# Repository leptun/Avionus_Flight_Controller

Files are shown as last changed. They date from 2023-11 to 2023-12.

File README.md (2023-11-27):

# Avionus_Flight_Controller

This repo contains the mainboard for the Avionus project, a semi-autonomous plane/drone. The project is work in progress 🚧.

Features:
- STM32F722ZE MCU with hardware float, 512KB of flash and 256KB of RAM
- 16MB total of external dual-mode QuadSPI (QPI) flash memory with XIP capability
- Full size SD card slot
- GPS (ublox MAX-M10S) with onboard antenna
- 9dof IMU ICM-20948
- LIDAR distance sensors with headers for:
  - LIDAR07-100W
  - VL53L1X
- 16 servo outputs (including at least one UART connection)
- RC remote input:
  - PPM interface
  - iBus interface
- LoRa 868MHz module using Semtech SX1262
- USB 2.0 FS with Type C connector (device only)
- Independent power domanins for the peripherals:
  - Power domains voltage measurement and monitoring
  - Current measurement of critical power domains
  - Very low power shutdown with wake from RTC
  - ESD protection of all IO
- STDC14 debugging header for STLINK-V3:
  - SWD
  - JTAG
  - SWO
  - UART

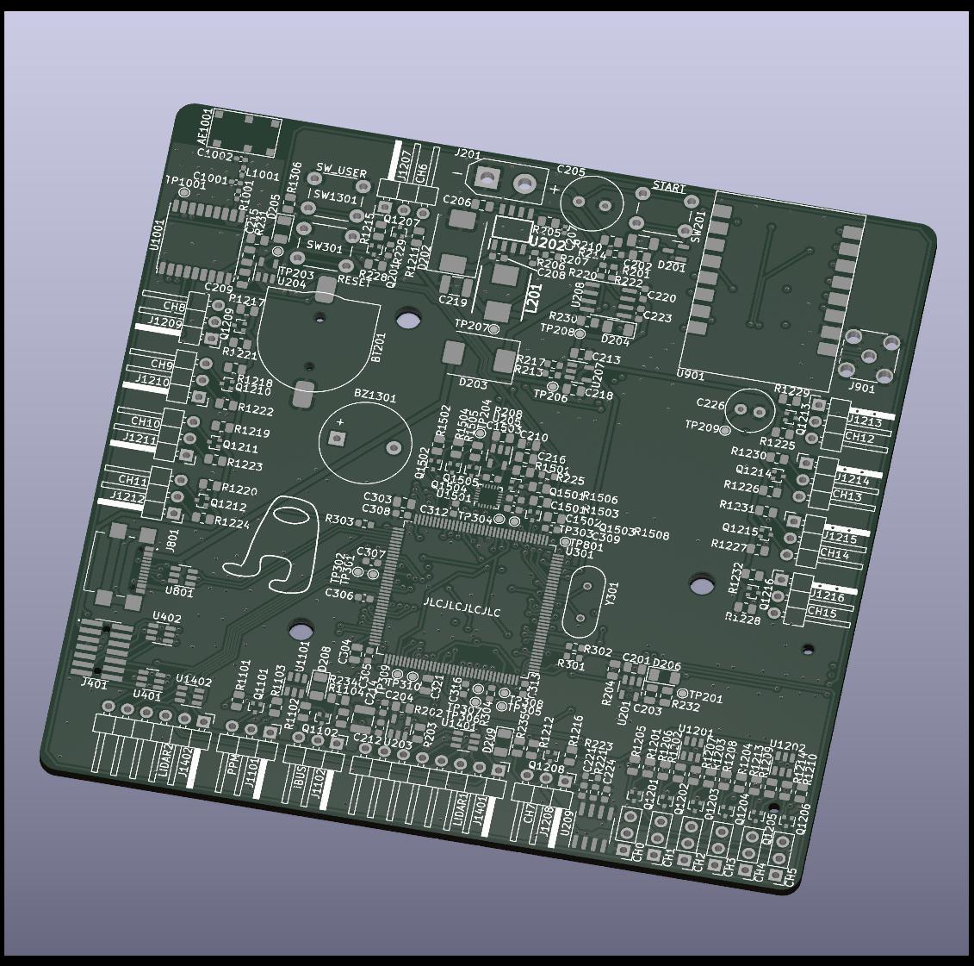
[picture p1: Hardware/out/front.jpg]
PCB_Front

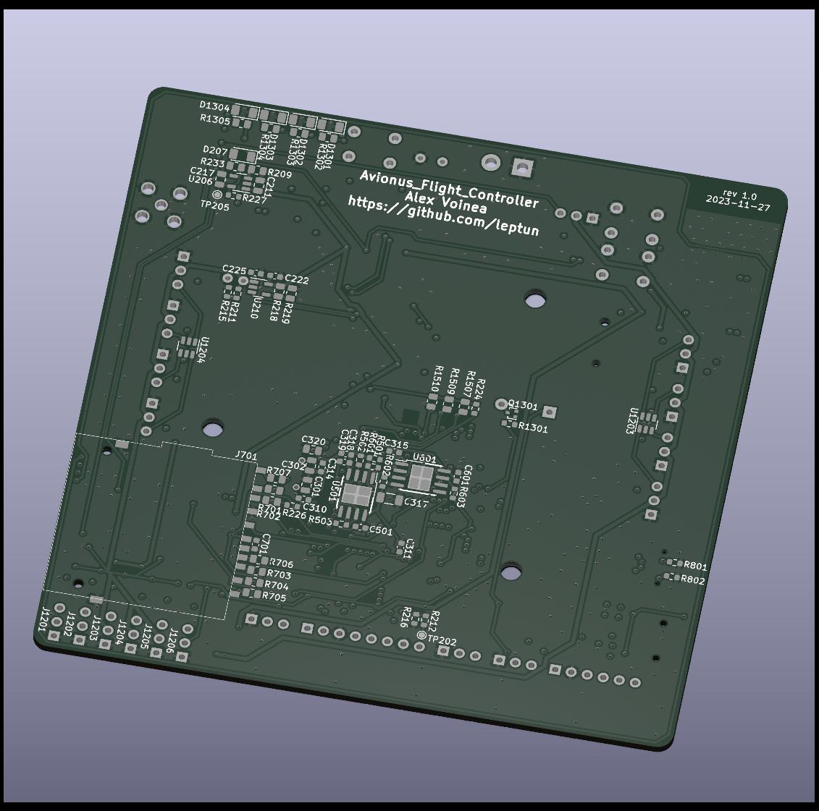
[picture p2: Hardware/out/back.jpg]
PCB_Back


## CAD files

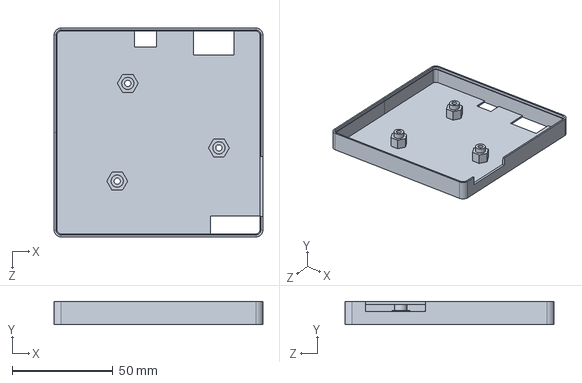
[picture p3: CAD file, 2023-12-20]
Prints/Avionus development backplate.SLDPRT
103.7 x 11.6 x 103.7 mm

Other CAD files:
Prints/Avionus development backplate.STL

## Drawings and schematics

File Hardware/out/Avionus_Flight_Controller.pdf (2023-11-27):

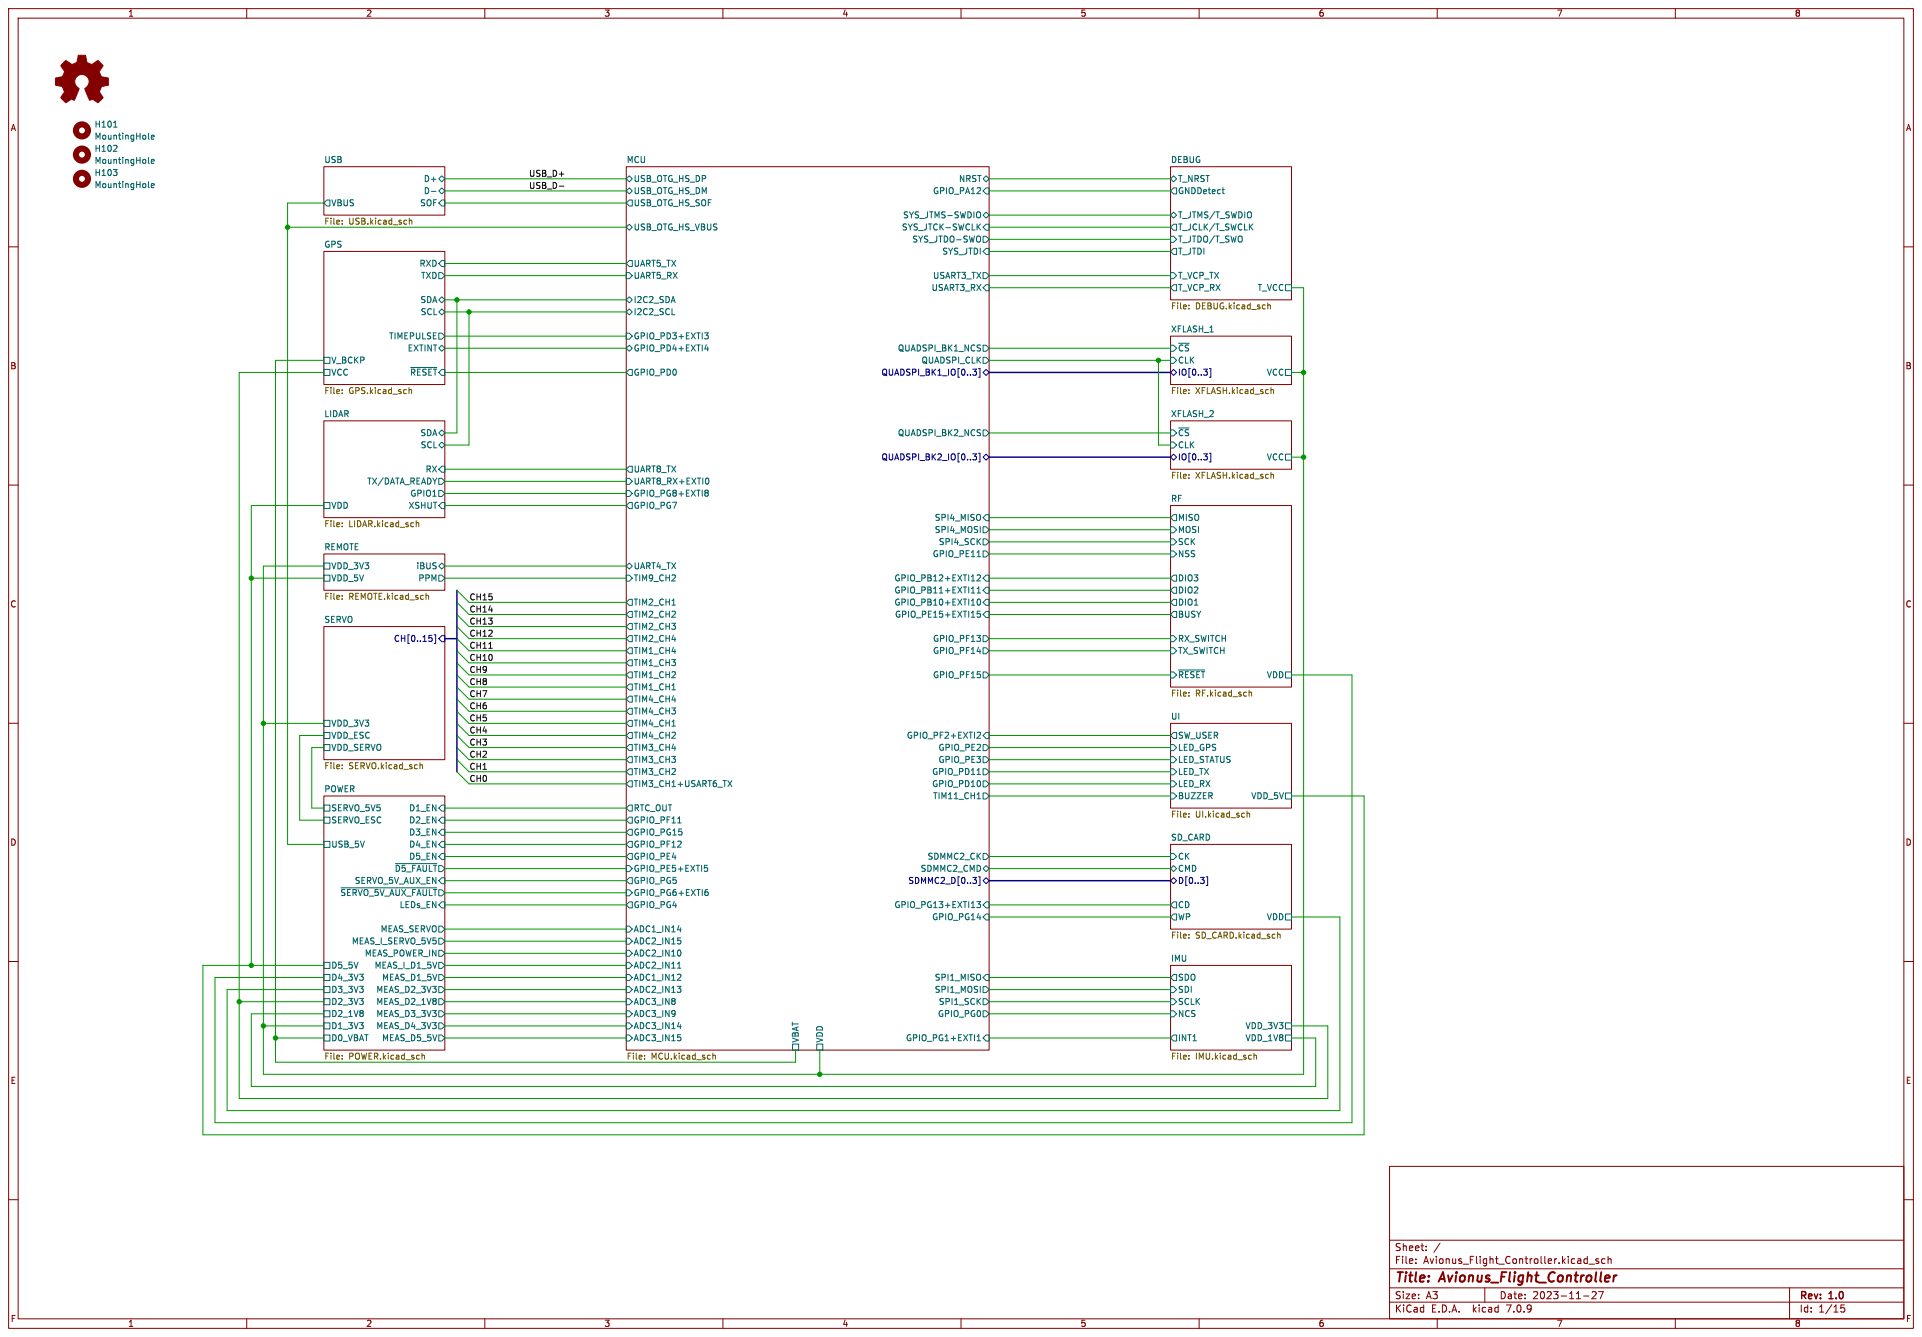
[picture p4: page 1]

GPIO_PA12 GPIO_PE2 GPIO_PG7 GPIO_PG8+EXTI8 MCU
SYS_JTDI QUADSPI_BK2_IO[0..3]
IO[0..3] XFLASH_1 File: XFLASH.kicad_sch SCK MISO MOSI NSS
IO[0..3] XFLASH_2 File: XFLASH.kicad_sch BUZZER

TXD GPS
EXTINT SCL ~{RESET} SDA RXD

DIO3 DIO2 DIO1 BUSY
VDD_5V UI File: UI.kicad_schVDD_1V8 NCS
File: IMU.kicad_sch CKCMD WP CD

Id: 1/15 Title: Avionus_Flight_Controller File: Avionus_Flight_Controller.kicad_sch Sheet: /

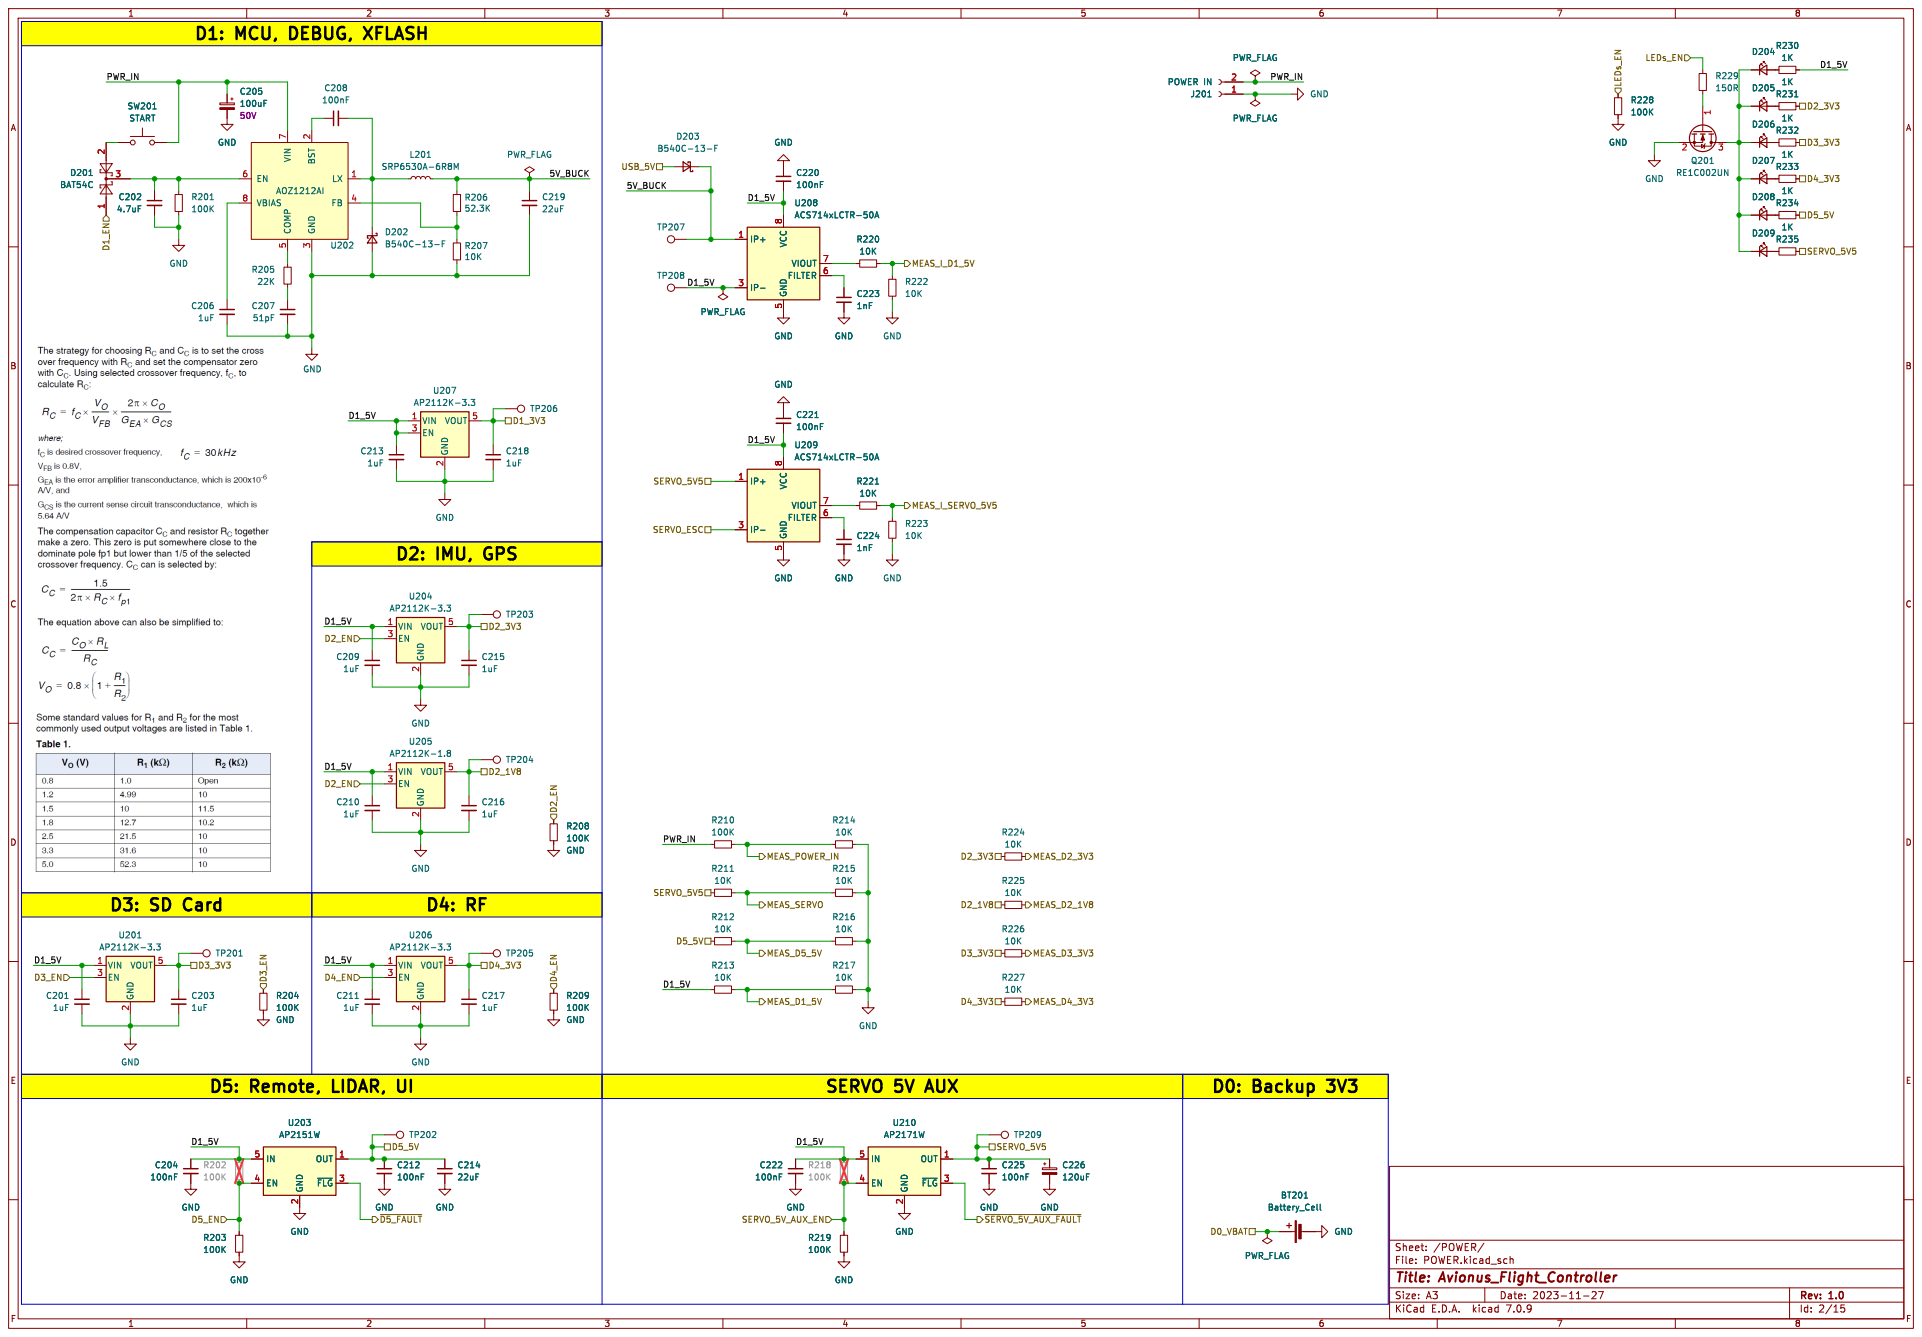
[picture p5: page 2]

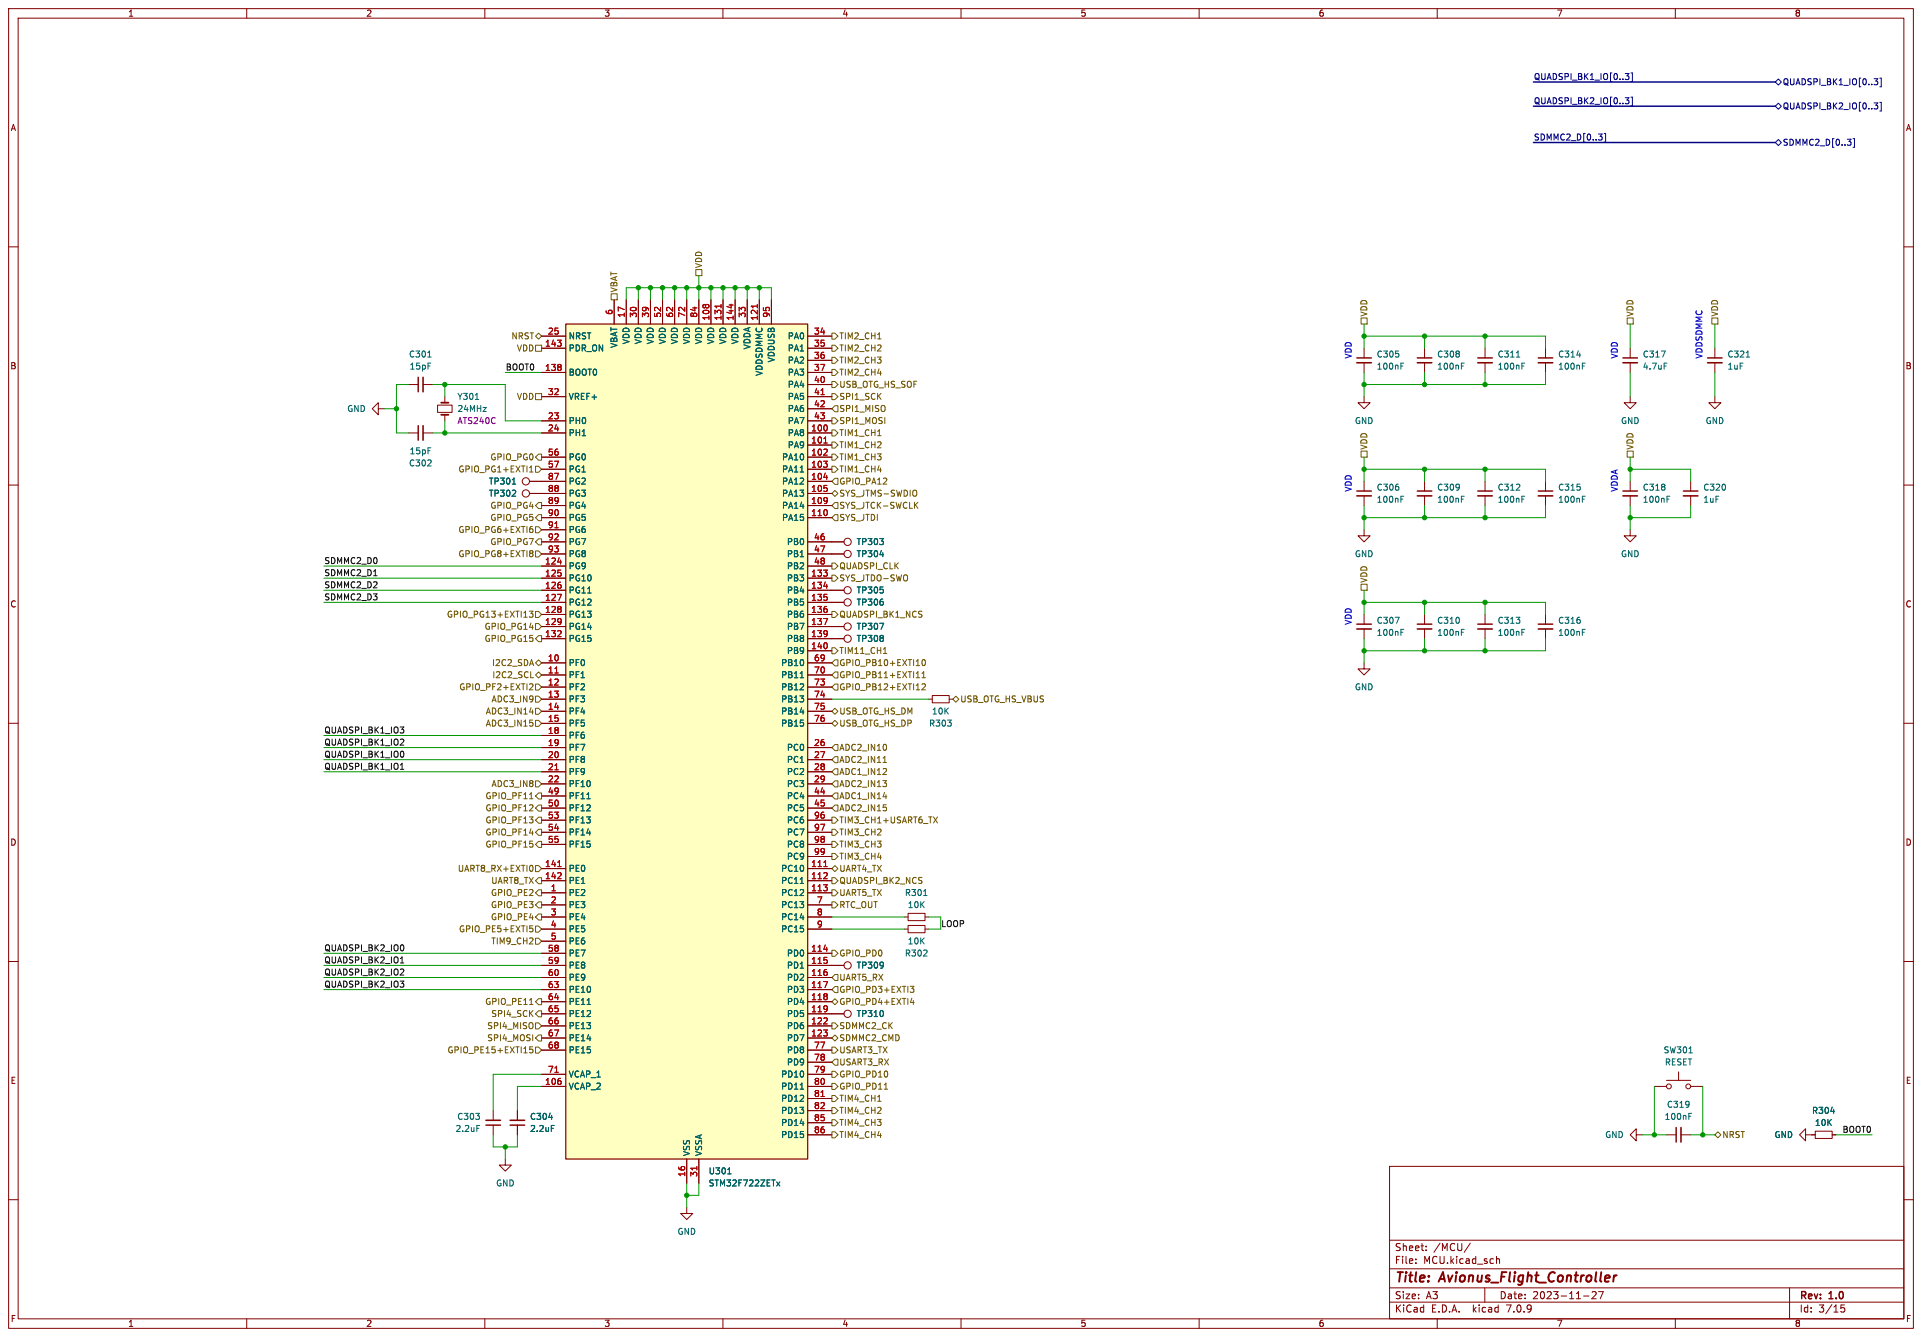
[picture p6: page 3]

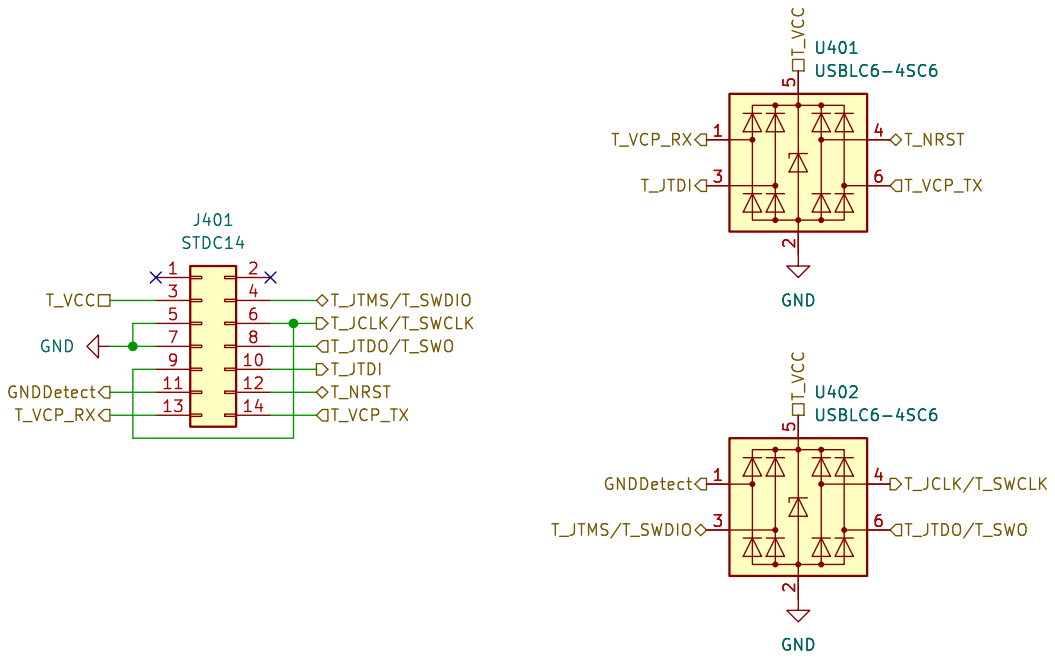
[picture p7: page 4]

Id: 4/15 Title: Avionus_Flight_Controller File: DEBUG.kicad_sch Sheet: /DEBUG/

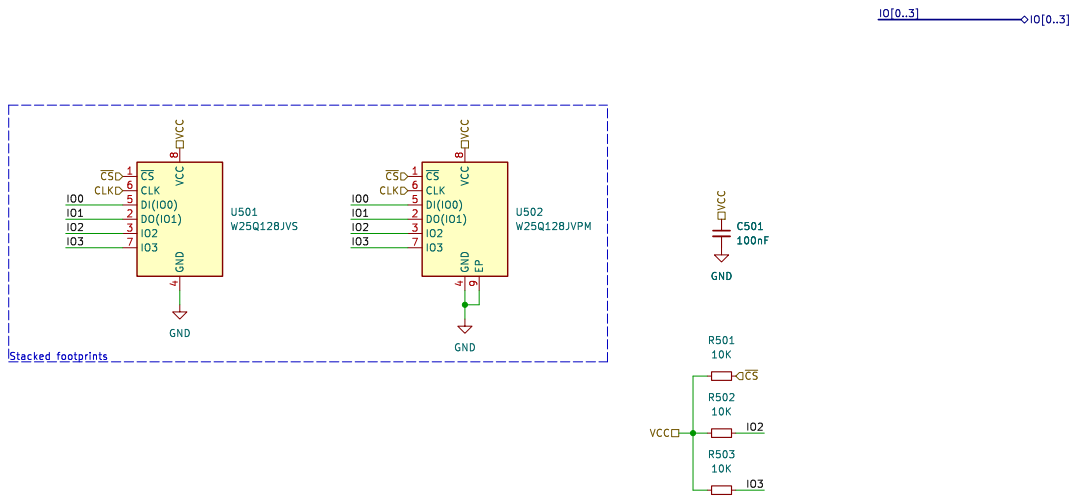
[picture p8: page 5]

Id: 5/15 Title: Avionus_Flight_Controller File: XFLASH.kicad_sch Sheet: /XFLASH_1/

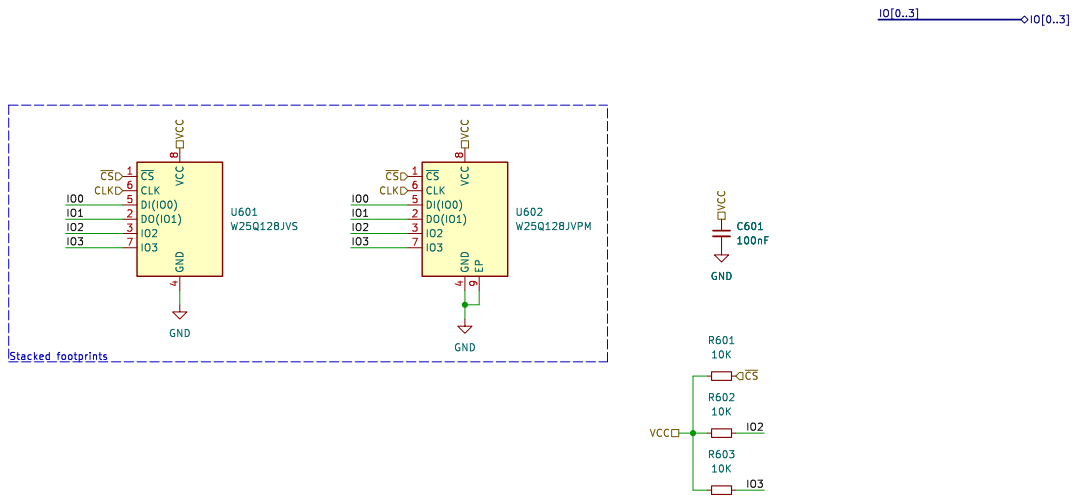
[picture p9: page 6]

Id: 6/15 Title: Avionus_Flight_Controller File: XFLASH.kicad_sch Sheet: /XFLASH_2/

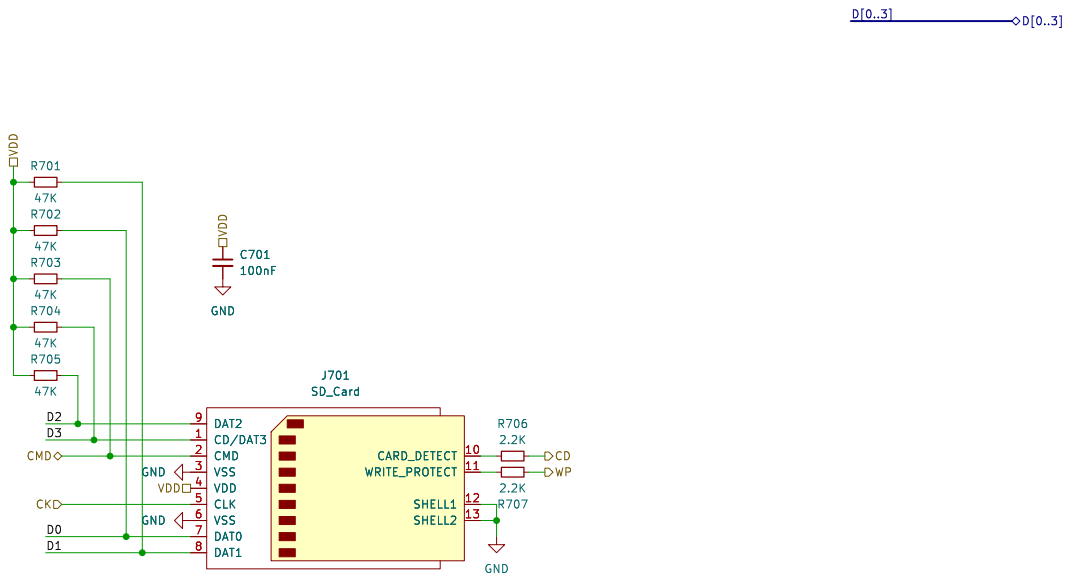
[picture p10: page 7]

Id: 7/15 Title: Avionus_Flight_Controller File: SD_CARD.kicad_sch Sheet: /SD_CARD/

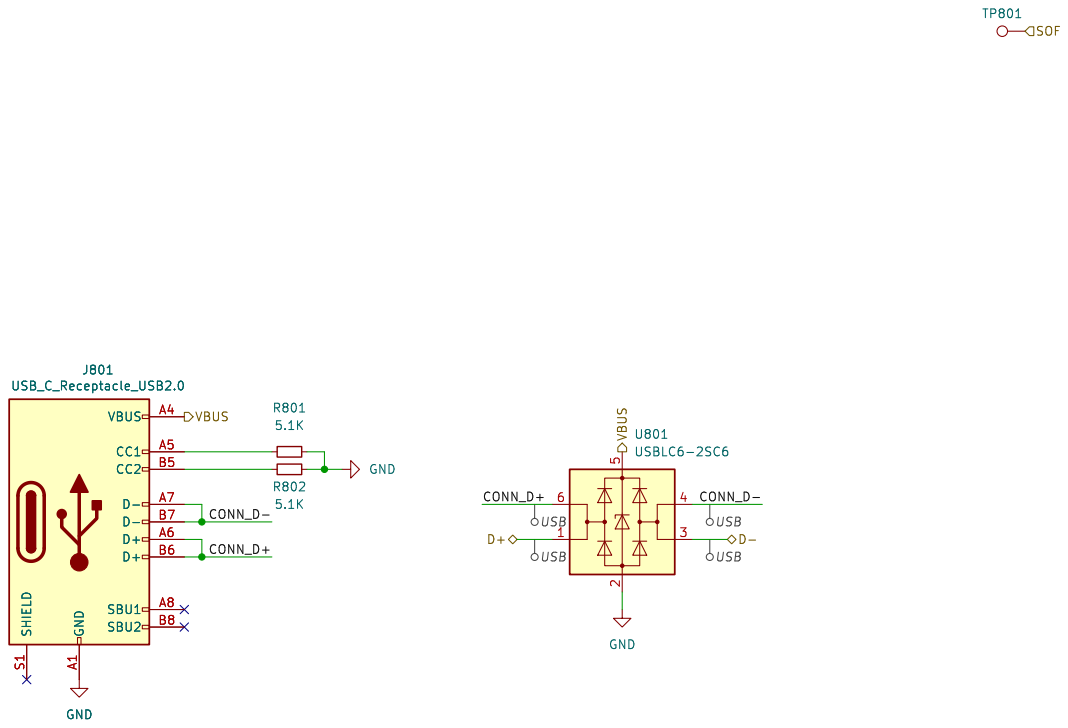
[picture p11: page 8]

Id: 8/15 Title: Avionus_Flight_Controller File: USB.kicad_sch Sheet: /USB/

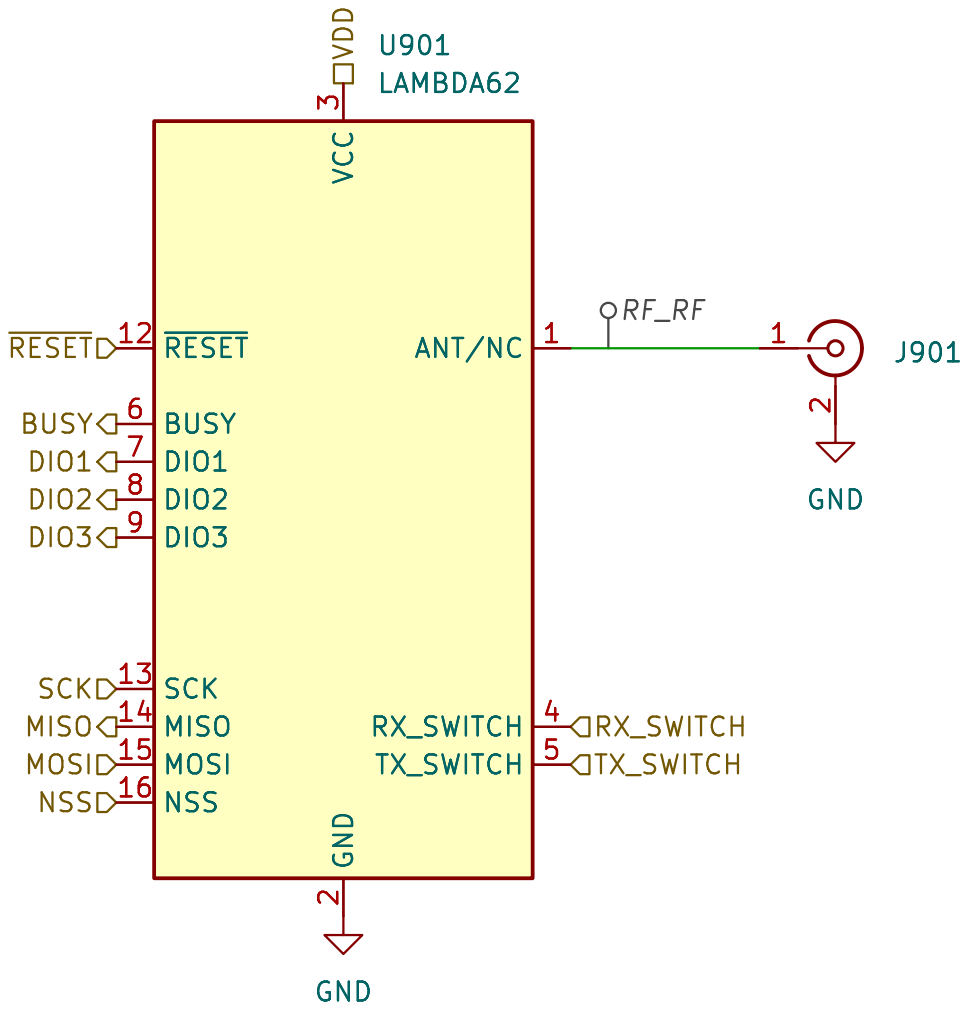
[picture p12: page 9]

Id: 9/15 Title: Avionus_Flight_Controller File: RF.kicad_sch Sheet: /RF/

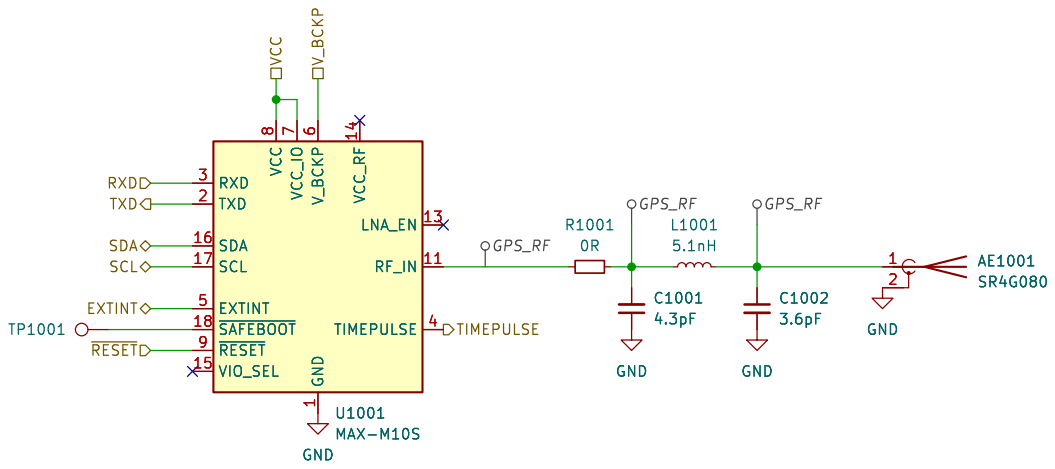
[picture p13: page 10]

TIMEPULSE GND
Id: 10/15 Title: Avionus_Flight_Controller File: GPS.kicad_sch Sheet: /GPS/ GND

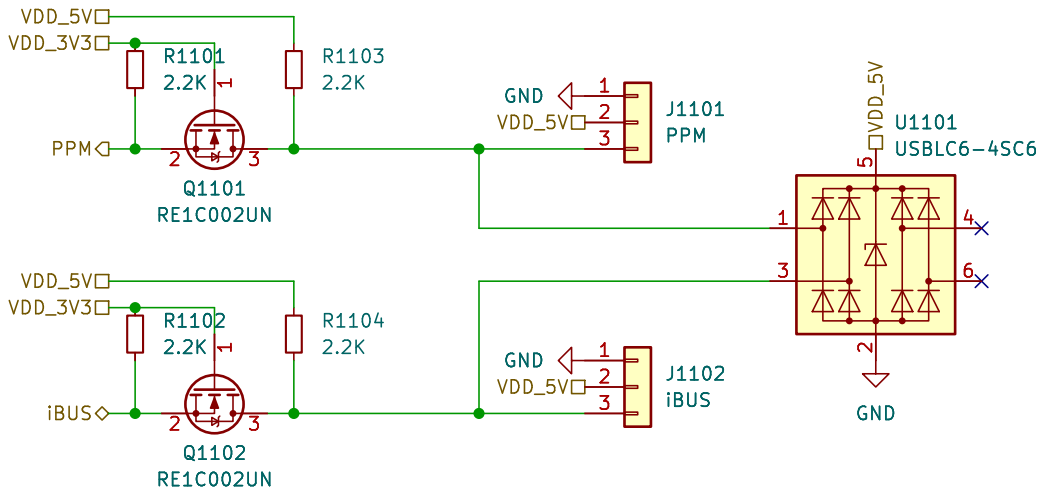
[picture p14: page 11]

Id: 11/15 Title: Avionus_Flight_Controller File: REMOTE.kicad_sch Sheet: /REMOTE/

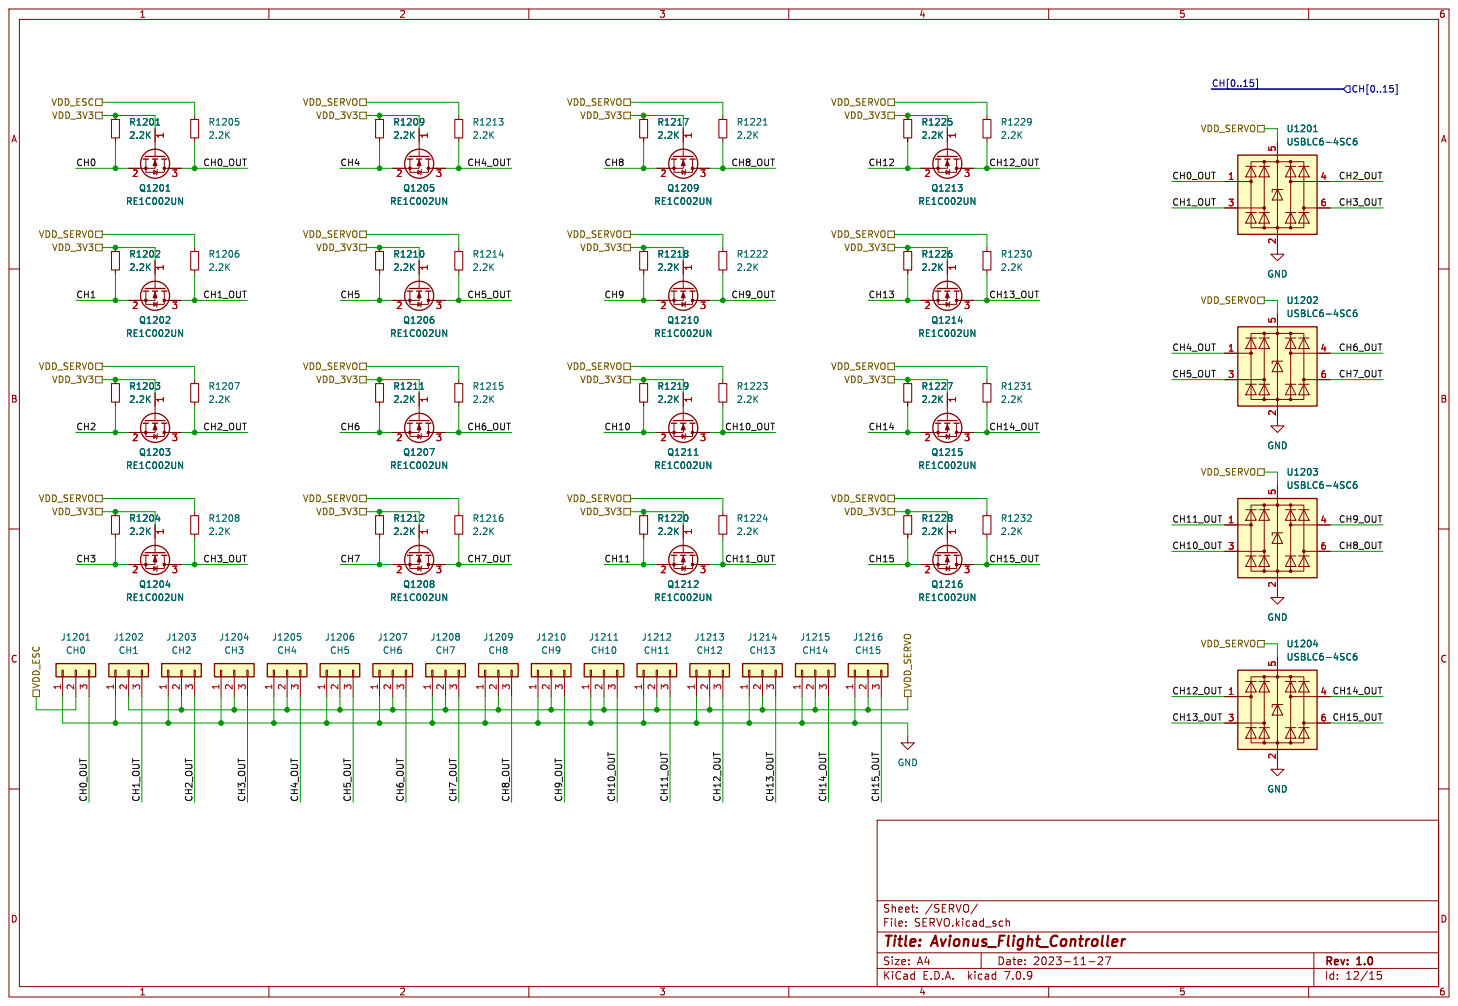
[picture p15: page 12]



Id: 14/15 Title: Avionus_Flight_Controller File: LIDAR.kicad_sch Sheet: /LIDAR/ GND GND
VDD


Id: 15/15 Title: Avionus_Flight_Controller File: IMU.kicad_sch Sheet: /IMU/

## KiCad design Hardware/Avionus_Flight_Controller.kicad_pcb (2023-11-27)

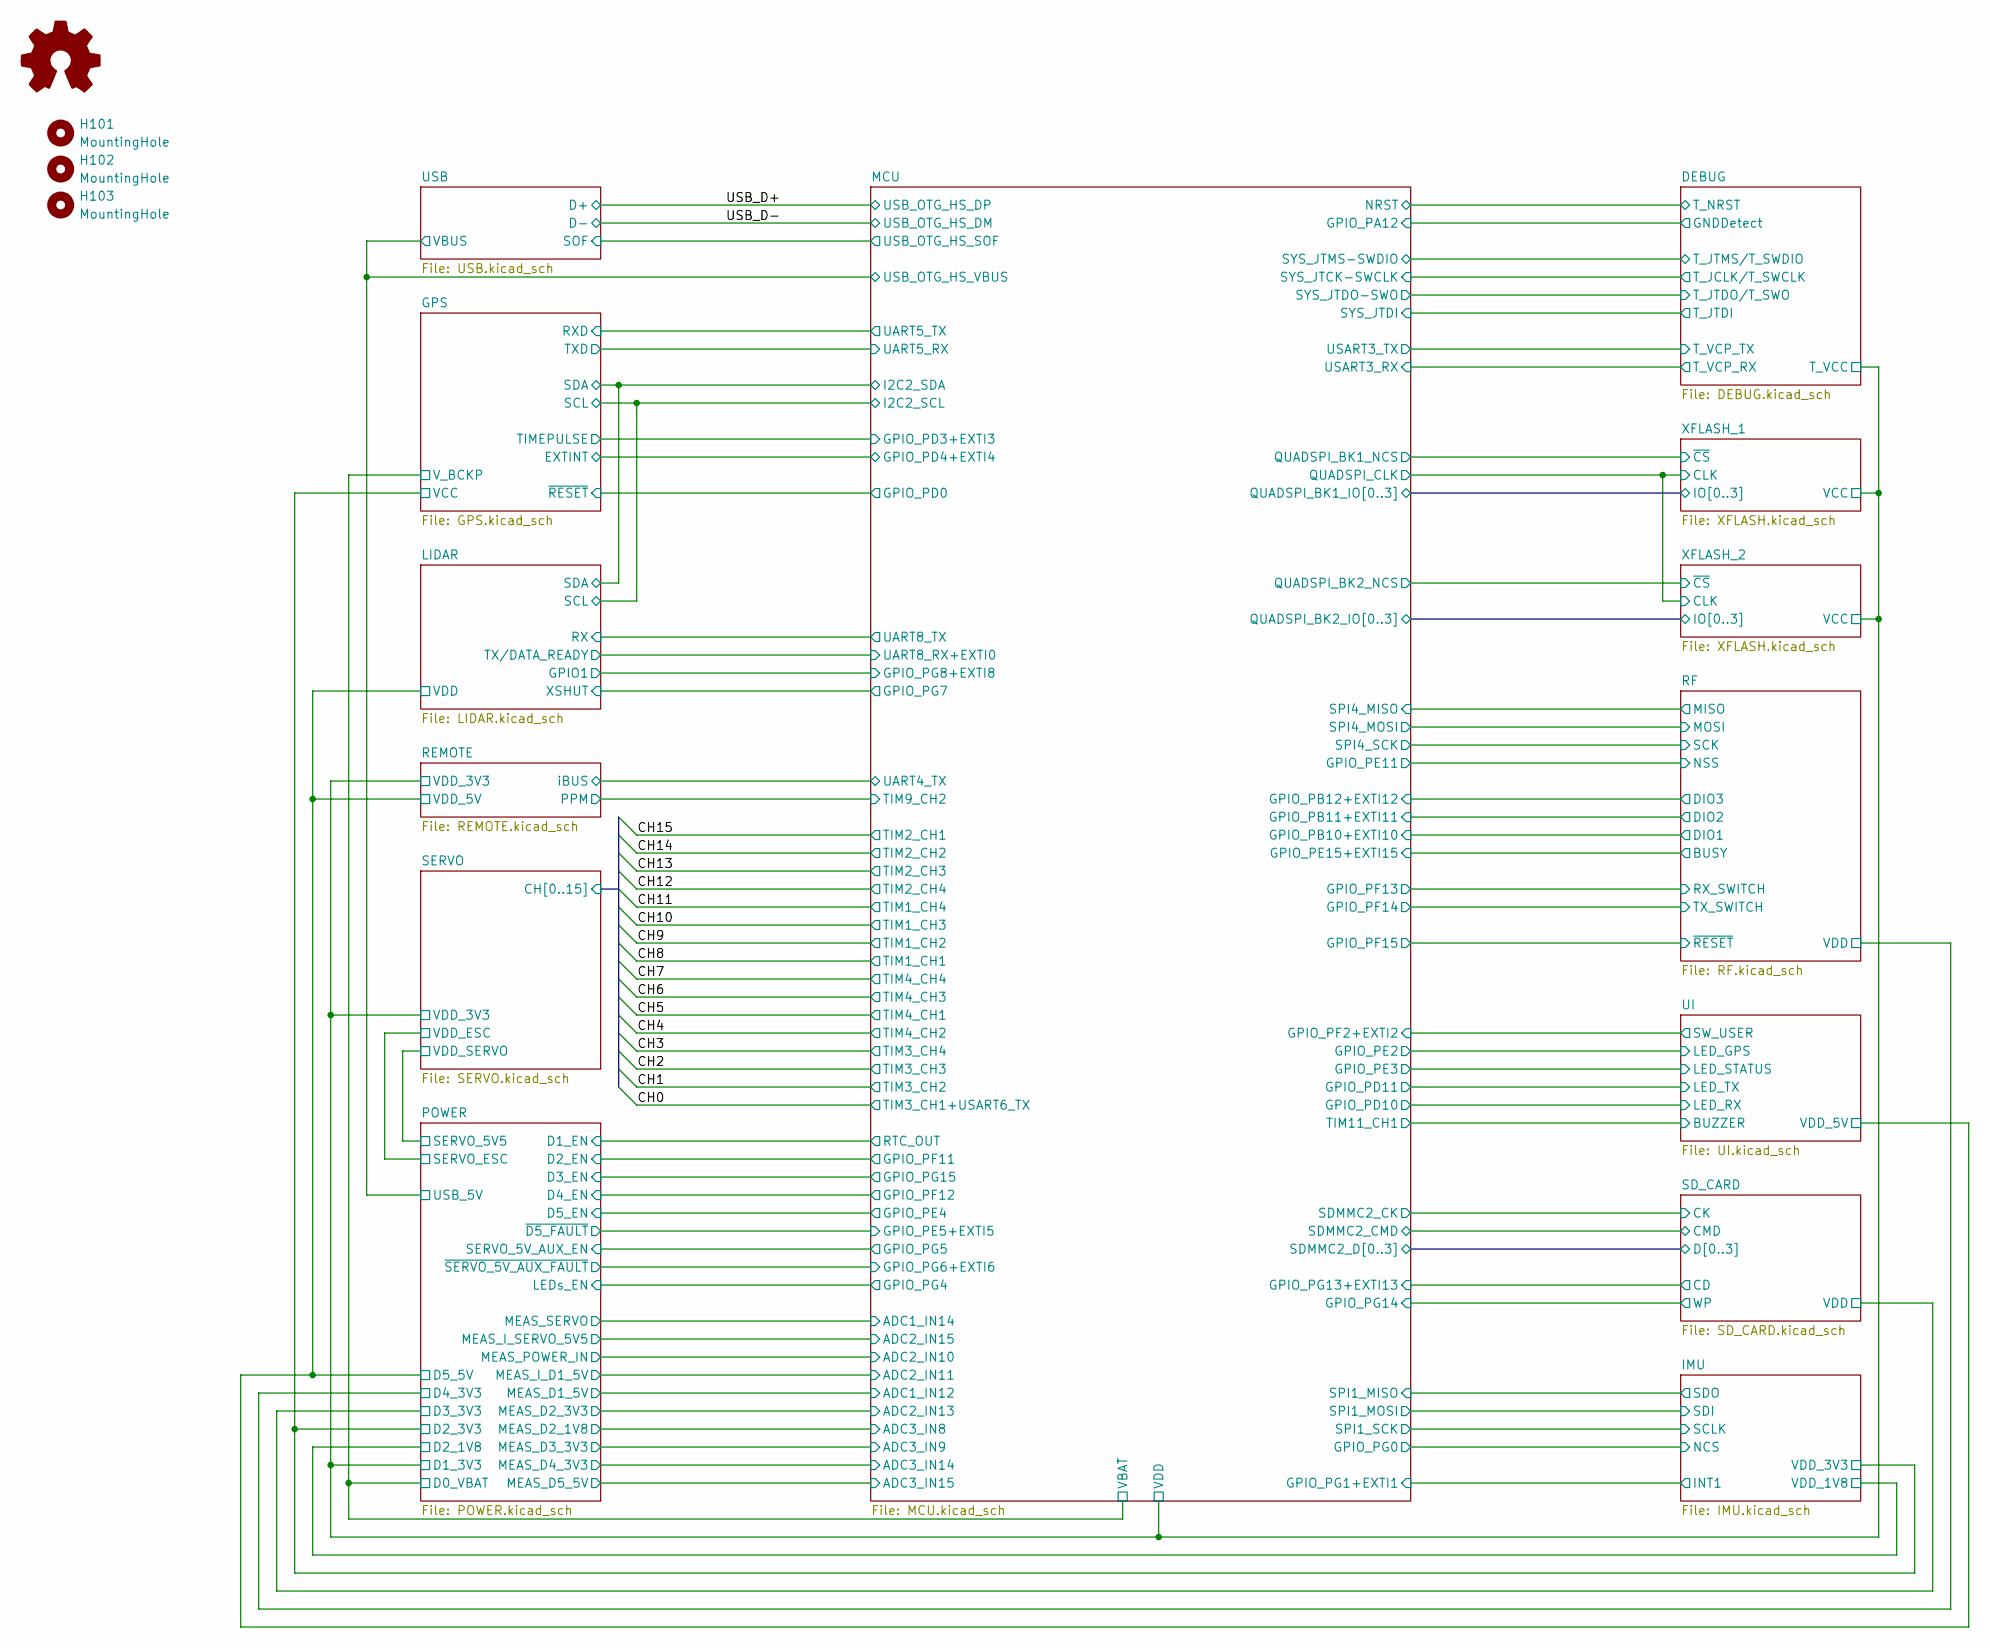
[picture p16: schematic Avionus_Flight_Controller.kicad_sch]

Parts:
H101, H102, H103: MountingHole; MountingHole_3.2mm_M3
SYM101: AMOGUS

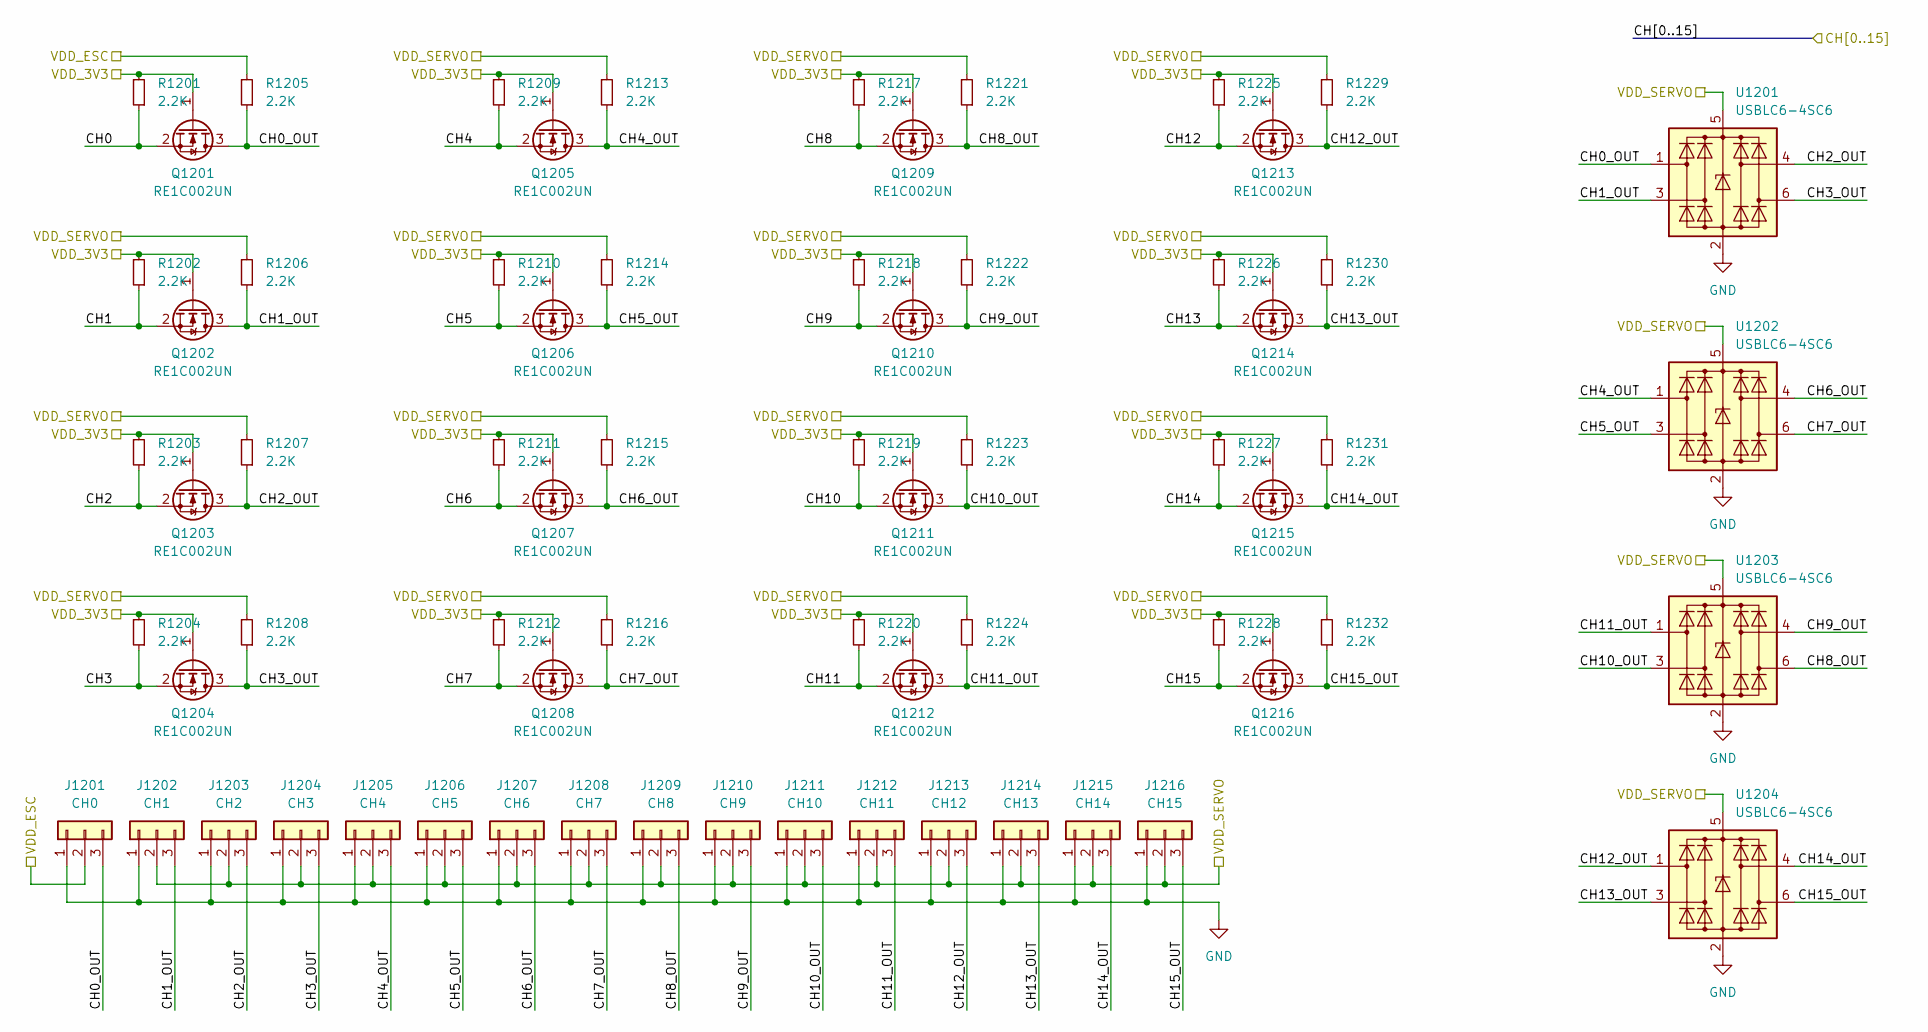
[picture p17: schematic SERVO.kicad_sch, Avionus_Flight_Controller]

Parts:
J1201: CH0; PinHeader_1x03_P2.54mm_Vertical
J1202: CH1; PinHeader_1x03_P2.54mm_Vertical
J1203: CH2; PinHeader_1x03_P2.54mm_Vertical
J1204: CH3; PinHeader_1x03_P2.54mm_Vertical
J1205: CH4; PinHeader_1x03_P2.54mm_Vertical
J1206: CH5; PinHeader_1x03_P2.54mm_Vertical
J1207: CH6; PinHeader_1x03_P2.54mm_Horizontal
J1208: CH7; PinHeader_1x03_P2.54mm_Horizontal
J1209: CH8; PinHeader_1x03_P2.54mm_Horizontal
J1210: CH9; PinHeader_1x03_P2.54mm_Horizontal
J1211: CH10; PinHeader_1x03_P2.54mm_Horizontal
J1212: CH11; PinHeader_1x03_P2.54mm_Horizontal
J1213: CH12; PinHeader_1x03_P2.54mm_Horizontal
J1214: CH13; PinHeader_1x03_P2.54mm_Horizontal
J1215: CH14; PinHeader_1x03_P2.54mm_Horizontal
J1216: CH15; PinHeader_1x03_P2.54mm_Horizontal
Q1201, Q1202, Q1203, Q1204, Q1205, Q1206, Q1207, Q1208, Q1209, Q1210, Q1211, Q1212, Q1213, Q1214, Q1215, Q1216: RE1C002UN; SOT-416
R1201, R1202, R1203, R1204, R1205, R1206, R1207, R1208, R1209, R1210, R1211, R1212, R1213, R1214, R1215, R1216, R1217, R1218, R1219, R1220, R1221, R1222, R1223, R1224, R1225, R1226, R1227, R1228, R1229, R1230, R1231, R1232: 2.2K; R_0805_2012Metric
U1201, U1202, U1203, U1204: USBLC6-4SC6; SOT-23-6

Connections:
/DEBUG/T_VCC: Q1201.1 (G), Q1202.1 (G), Q1203.1 (G), Q1204.1 (G), Q1205.1 (G), Q1206.1 (G), Q1207.1 (G), Q1208.1 (G), Q1209.1 (G), Q1210.1 (G), Q1211.1 (G), Q1212.1 (G), Q1213.1 (G), Q1214.1 (G), Q1215.1 (G), Q1216.1 (G), R1201.2, R1202.2, R1203.2, R1204.2, R1209.2, R1210.2, R1211.2, R1212.2, R1217.2, R1218.2, R1219.2, R1220.2, R1225.2, R1226.2, R1227.2, R1228.2; also elsewhere on the board
/POWER/SERVO_5V5: J1202.2, J1203.2, J1204.2, J1205.2, J1206.2, J1207.2, J1208.2, J1209.2, J1210.2, J1211.2, J1212.2, J1213.2, J1214.2, J1215.2, J1216.2, R1206.2, R1207.2, R1208.2, R1213.2, R1214.2, R1215.2, R1216.2, R1221.2, R1222.2, R1223.2, R1224.2, R1229.2, R1230.2, R1231.2, R1232.2, U1201.5 (VBUS), U1202.5 (VBUS), U1203.5 (VBUS), U1204.5 (VBUS); also elsewhere on the board
/POWER/SERVO_ESC: J1201.2, R1205.2; also elsewhere on the board
/SERVO/CH0: Q1201.2 (S), R1201.1; also elsewhere on the board
/SERVO/CH0_OUT: J1201.3, Q1201.3 (D), R1205.1, U1201.1 (I/O1)
/SERVO/CH1: Q1202.2 (S), R1202.1; also elsewhere on the board
/SERVO/CH1_OUT: J1202.3, Q1202.3 (D), R1206.1, U1201.3 (I/O2)
/SERVO/CH2: Q1203.2 (S), R1203.1; also elsewhere on the board
/SERVO/CH2_OUT: J1203.3, Q1203.3 (D), R1207.1, U1201.4 (I/O3)
/SERVO/CH3: Q1204.2 (S), R1204.1; also elsewhere on the board
/SERVO/CH3_OUT: J1204.3, Q1204.3 (D), R1208.1, U1201.6 (I/O4)
/SERVO/CH4: Q1205.2 (S), R1209.1; also elsewhere on the board
/SERVO/CH4_OUT: J1205.3, Q1205.3 (D), R1213.1, U1202.1 (I/O1)
/SERVO/CH5: Q1206.2 (S), R1210.1; also elsewhere on the board
/SERVO/CH5_OUT: J1206.3, Q1206.3 (D), R1214.1, U1202.3 (I/O2)
/SERVO/CH6: Q1207.2 (S), R1211.1; also elsewhere on the board
/SERVO/CH6_OUT: J1207.3, Q1207.3 (D), R1215.1, U1202.4 (I/O3)
/SERVO/CH7: Q1208.2 (S), R1212.1; also elsewhere on the board
/SERVO/CH7_OUT: J1208.3, Q1208.3 (D), R1216.1, U1202.6 (I/O4)
/SERVO/CH8: Q1209.2 (S), R1217.1; also elsewhere on the board
/SERVO/CH8_OUT: J1209.3, Q1209.3 (D), R1221.1, U1203.6 (I/O4)
/SERVO/CH9: Q1210.2 (S), R1218.1; also elsewhere on the board
/SERVO/CH9_OUT: J1210.3, Q1210.3 (D), R1222.1, U1203.4 (I/O3)
/SERVO/CH10: Q1211.2 (S), R1219.1; also elsewhere on the board
/SERVO/CH10_OUT: J1211.3, Q1211.3 (D), R1223.1, U1203.3 (I/O2)
/SERVO/CH11: Q1212.2 (S), R1220.1; also elsewhere on the board
/SERVO/CH11_OUT: J1212.3, Q1212.3 (D), R1224.1, U1203.1 (I/O1)
/SERVO/CH12: Q1213.2 (S), R1225.1; also elsewhere on the board
/SERVO/CH12_OUT: J1213.3, Q1213.3 (D), R1229.1, U1204.1 (I/O1)
/SERVO/CH13: Q1214.2 (S), R1226.1; also elsewhere on the board
/SERVO/CH13_OUT: J1214.3, Q1214.3 (D), R1230.1, U1204.3 (I/O2)
/SERVO/CH14: Q1215.2 (S), R1227.1; also elsewhere on the board
/SERVO/CH14_OUT: J1215.3, Q1215.3 (D), R1231.1, U1204.4 (I/O3)
/SERVO/CH15: Q1216.2 (S), R1228.1; also elsewhere on the board
/SERVO/CH15_OUT: J1216.3, Q1216.3 (D), R1232.1, U1204.6 (I/O4)
GND: J1201.1, J1202.1, J1203.1, J1204.1, J1205.1, J1206.1, J1207.1, J1208.1, J1209.1, J1210.1, J1211.1, J1212.1, J1213.1, J1214.1, J1215.1, J1216.1, U1201.2 (GND), U1202.2 (GND), U1203.2 (GND), U1204.2 (GND); also elsewhere on the board

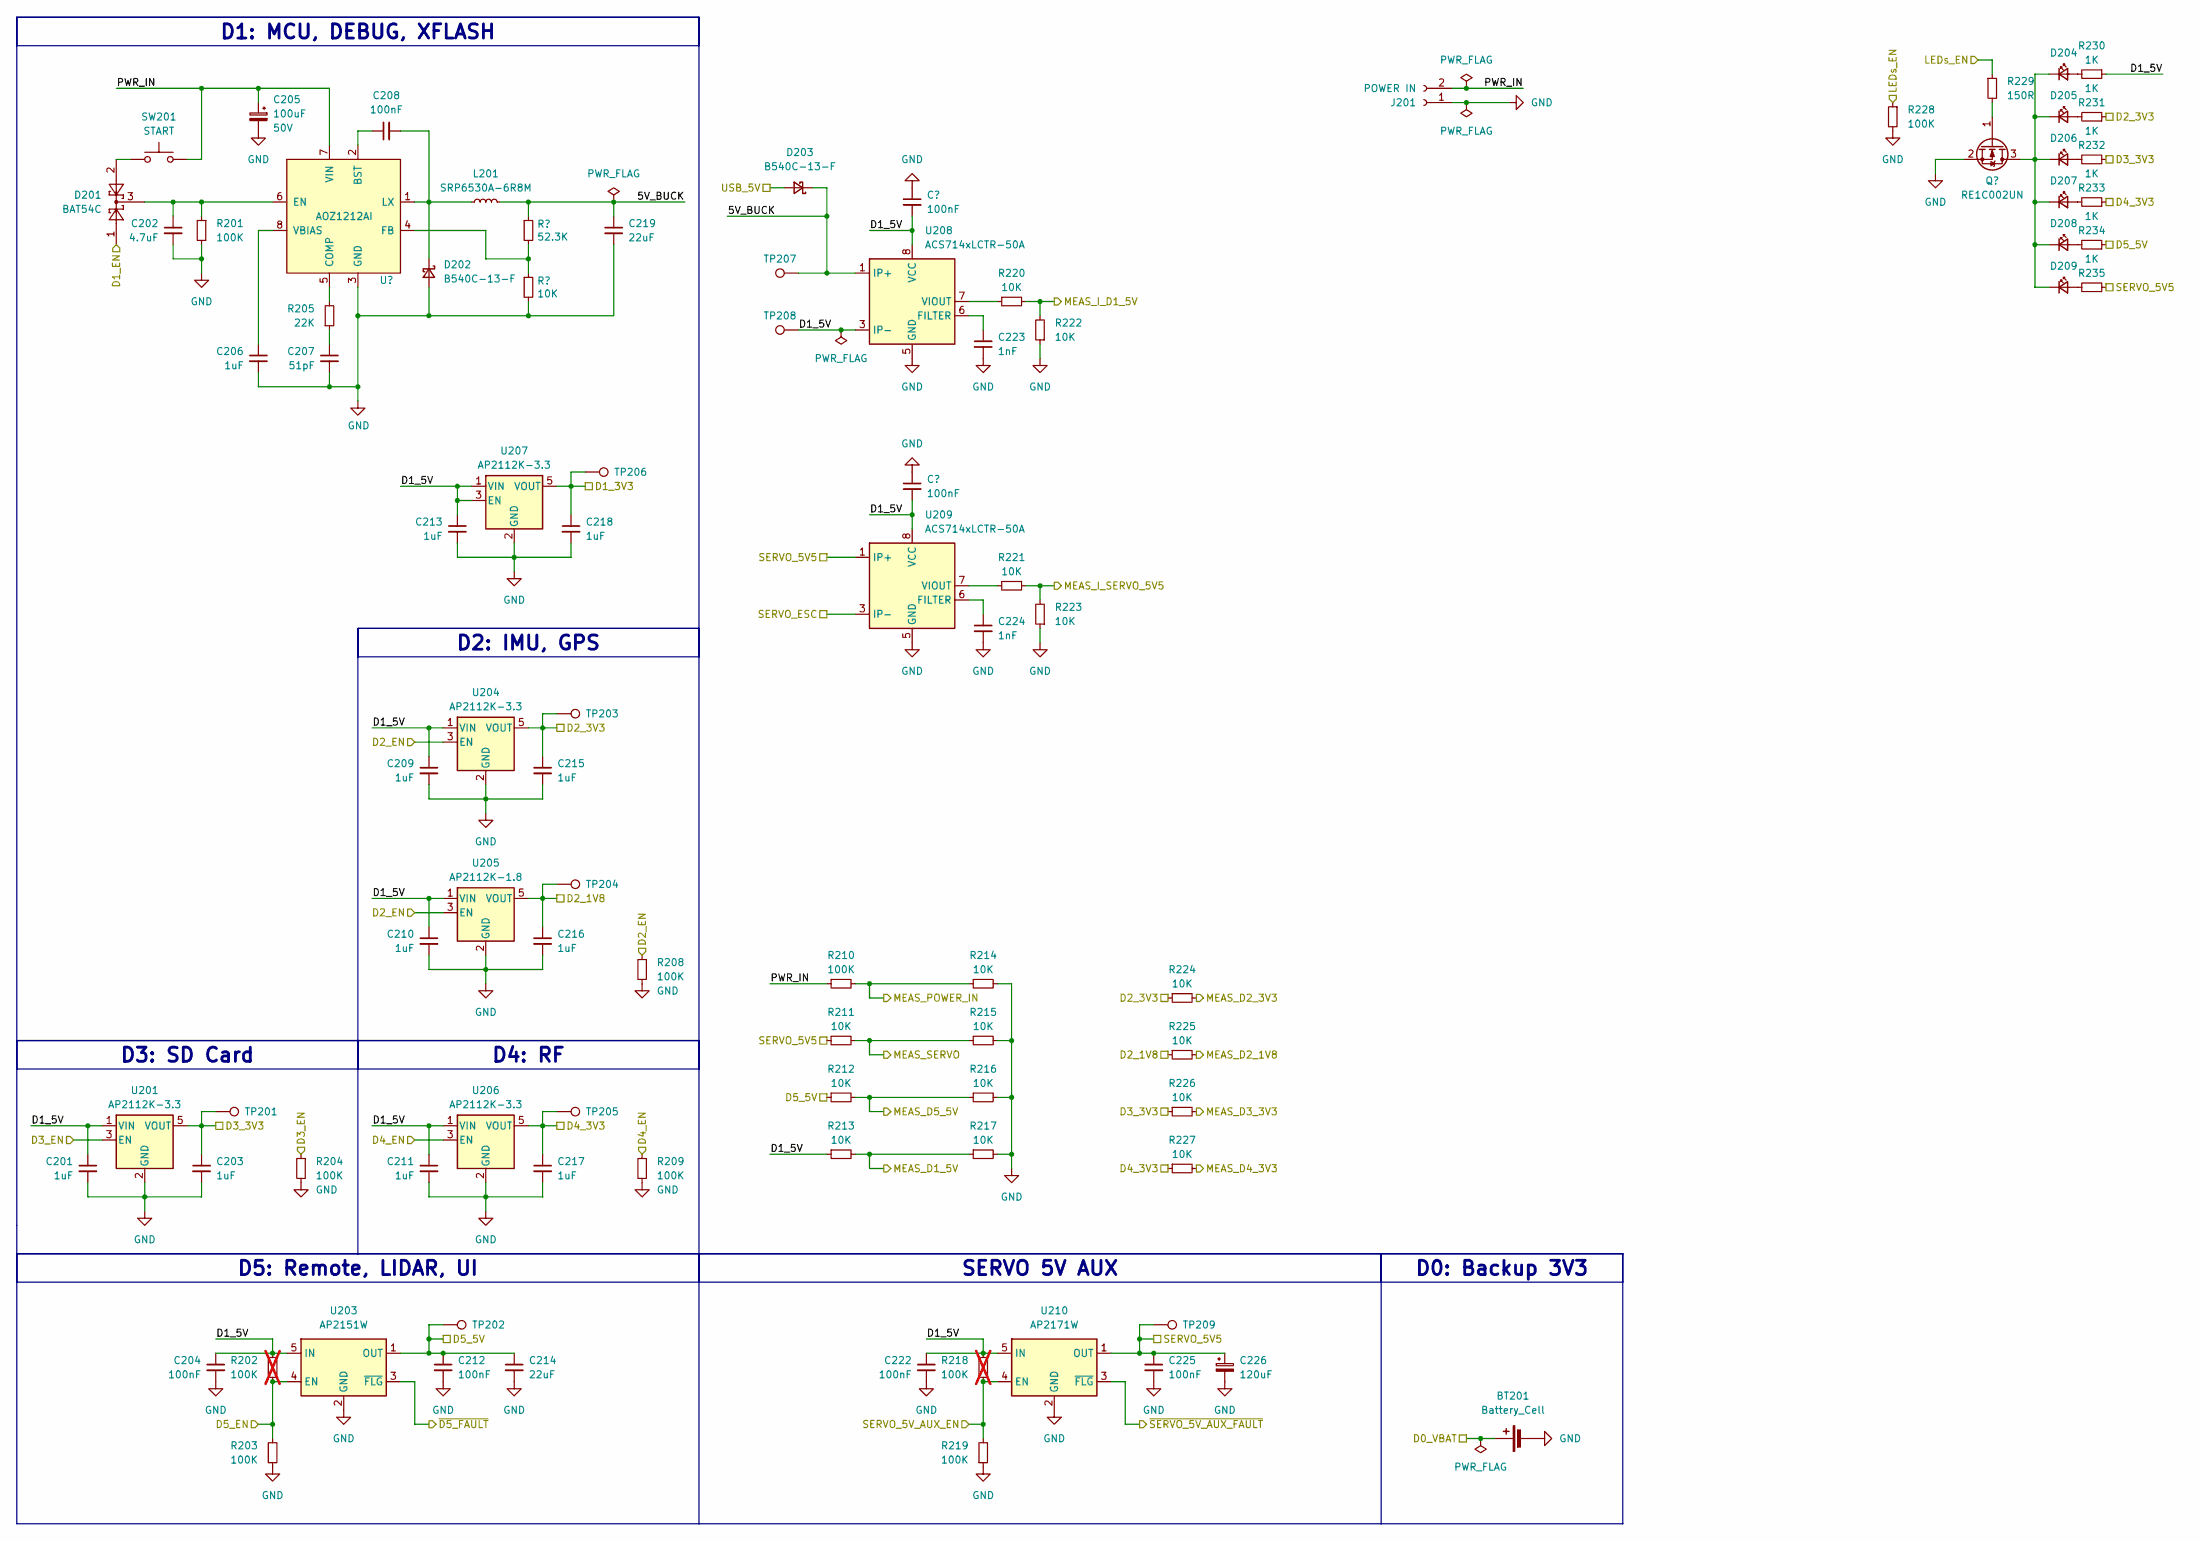
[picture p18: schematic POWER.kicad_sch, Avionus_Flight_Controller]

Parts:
BT201: Battery_Cell; DS1092-12-N8S
C201, C203, C206, C209, C210, C211, C213, C215, C216, C217, C218: 1uF; C_0805_2012Metric
C202: 4.7uF; C_1206_3216Metric
C204, C208, C212, C220, C221, C222, C225: 100nF; C_0603_1608Metric
C205: 100uF; C_Radial_D8.0mm_H11.5mm_P3.50mm; Rating 50V
C207: 51pF; C_0402_1005Metric
C214, C219: 22uF; C_1210_3225Metric
C223, C224: 1nF; C_0603_1608Metric
C226: 120uF; C_Radial_D6.3mm_H11.0mm_P2.50mm
D201: BAT54C; SOT-23
D202, D203: B540C-13-F; D_SMC
D204, D205, D206, D207, D208, D209: LED_1206_3216Metric
J201: POWER IN; AMASS_XT30UPB-M_1x02_P5.0mm_Vertical
L201: SRP6530A-6R8M
Q201: RE1C002UN; SOT-416
R201, R203, R204, R208, R209, R210, R219, R228: 100K; R_0805_2012Metric
R202, R218: 100K; R_0805_2012Metric; not fitted
R205: 22K; R_0805_2012Metric
R206: 52.3K; R_0603_1608Metric
R207, R211, R212, R213, R214, R215, R216, R217, R220, R221, R222, R223, R224, R225, R226, R227: 10K; R_0603_1608Metric
R229: 150R; R_0603_1608Metric
R230, R231, R232, R233, R234, R235: 1K; R_0805_2012Metric
SW201: START; SW_PUSH_6mm_H5mm
TP201, TP202, TP203, TP204, TP205, TP206, TP207, TP208, TP209: TestPoint_Pad_D1.0mm
U201, U204, U206, U207: AP2112K-3.3; SOT-23-5
U202: AOZ1212AI
U203: AP2151W; SOT-23-5
U205: AP2112K-1.8; SOT-23-5
U208, U209: ACS714xLCTR-50A; SOIC-8_3.9x4.9mm_P1.27mm
U210: AP2171W; SOT-23-5

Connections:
/DEBUG/T_VCC: C218.1, TP206.1, U207.5 (VOUT); also elsewhere on the board
/GPS/VCC: C215.1, R224.1, R231.1, TP203.1, U204.5 (VOUT); also elsewhere on the board
/GPS/V_BCKP: BT201.1 (+); also elsewhere on the board
/IMU/VDD_1V8: C216.1, R225.1, TP204.1, U205.5 (VOUT); also elsewhere on the board
/MCU/ADC1_IN12: R213.2, R217.1; also elsewhere on the board
/MCU/ADC1_IN14: R211.2, R215.1; also elsewhere on the board
/MCU/ADC2_IN10: R210.2, R214.1; also elsewhere on the board
/MCU/ADC2_IN11: R220.2, R222.2; also elsewhere on the board
/MCU/ADC2_IN13: R224.2; also elsewhere on the board
/MCU/ADC2_IN15: R221.2, R223.2; also elsewhere on the board
/MCU/ADC3_IN8: R225.2; also elsewhere on the board
/MCU/ADC3_IN9: R226.2; also elsewhere on the board
/MCU/ADC3_IN14: R227.2; also elsewhere on the board
/MCU/ADC3_IN15: R212.2, R216.1; also elsewhere on the board
/MCU/GPIO_PE4: R202.1, R203.2, U203.4 (EN); also elsewhere on the board
/MCU/GPIO_PE5+EXTI5: U203.3 (~FLG); also elsewhere on the board
/MCU/GPIO_PF11: R208.1, U204.3 (EN), U205.3 (EN); also elsewhere on the board
/MCU/GPIO_PF12: R209.1, U206.3 (EN); also elsewhere on the board
/MCU/GPIO_PG4: R228.1, R229.1; also elsewhere on the board
/MCU/GPIO_PG5: R218.1, R219.2, U210.4 (EN); also elsewhere on the board
/MCU/GPIO_PG6+EXTI6: U210.3 (~FLG); also elsewhere on the board
/MCU/GPIO_PG15: R204.1, U201.3 (EN); also elsewhere on the board
/MCU/RTC_OUT: D201.1; also elsewhere on the board
/POWER/5V_BUCK: C219.1, D203.1 (K), L201.2, R206.1, TP207.1, U208.1 (IP+), U208.2 (IP+)
/POWER/D1_5V: C201.1, C204.1, C209.1, C210.1, C211.1, C213.1, C220.2, C221.2, C222.1, R202.2, R213.1, R218.2, R230.1, TP208.1, U201.1 (VIN), U203.5 (IN), U204.1 (VIN), U205.1 (VIN), U206.1 (VIN), U207.1 (VIN), U207.3 (EN), U208.3 (IP-), U208.4 (IP-), U208.8 (VCC), U209.8 (VCC), U210.5 (IN)
/POWER/D3_3V3: C203.1, R226.1, R232.1, TP201.1, U201.5 (VOUT); also elsewhere on the board
/POWER/D4_3V3: C217.1, R227.1, R233.1, TP205.1, U206.5 (VOUT); also elsewhere on the board
/POWER/PWR_IN: C205.1, J201.2, R210.1, SW201.2, U202.7 (VIN)
/POWER/SERVO_5V5: C225.1, C226.1, R211.1, R235.1, TP209.1, U209.1 (IP+), U209.2 (IP+), U210.1 (OUT); also elsewhere on the board
/POWER/SERVO_ESC: U209.3 (IP-), U209.4 (IP-); also elsewhere on the board
GND: BT201.2 (-), C201.2, C202.2, C203.2, C204.2, C205.2, C206.2, C207.2, C209.2, C210.2, C211.2, C212.2, C213.2, C214.2, C215.2, C216.2, C217.2, C218.2, C219.2, C220.1, C221.1, C222.2, C223.2, C224.2, C225.2, C226.2, D202.2 (A), J201.1, Q201.2 (S), R201.2, R203.1, R204.2, R207.2, R208.2, R209.2, R214.2, R215.2, R216.2, R217.2, R219.1, R222.1, R223.1, R228.2, U201.2 (GND), U202.3 (GND), U203.2 (GND), U204.2 (GND), U205.2 (GND), U206.2 (GND), U207.2 (GND), U208.5 (GND), U209.5 (GND), U210.2 (GND); also elsewhere on the board
unnamed: C207.1, R205.1
unnamed: D201.2, SW201.1
unnamed: C208.2, D202.1 (K), L201.1, U202.1 (LX)
unnamed: D204.2 (A), R230.2
unnamed: D204.1 (K), D205.1 (K), D206.1 (K), D207.1 (K), D208.1 (K), D209.1 (K), Q201.3 (D)
unnamed: D205.2 (A), R231.2
unnamed: D206.2 (A), R232.2
unnamed: D207.2 (A), R233.2
unnamed: D208.2 (A), R234.2
unnamed: D209.2 (A), R235.2
unnamed: Q201.1 (G), R229.2
unnamed: C208.1, U202.2 (BST)
unnamed: R205.2, U202.5 (COMP)
unnamed: C202.1, D201.3, R201.1, U202.6 (EN)
unnamed: R206.2, R207.1, U202.4 (FB)
unnamed: C206.1, U202.8 (VBIAS)
unnamed: C223.1, U208.6 (FILTER)
unnamed: R220.1, U208.7 (VIOUT)
unnamed: C224.1, U209.6 (FILTER)
unnamed: R221.1, U209.7 (VIOUT)

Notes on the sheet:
D5: Remote, LIDAR, UI
SERVO 5V AUX
D0: Backup 3V3
D3: SD Card
D4: RF
D1: MCU, DEBUG, XFLASH
D2: IMU, GPS

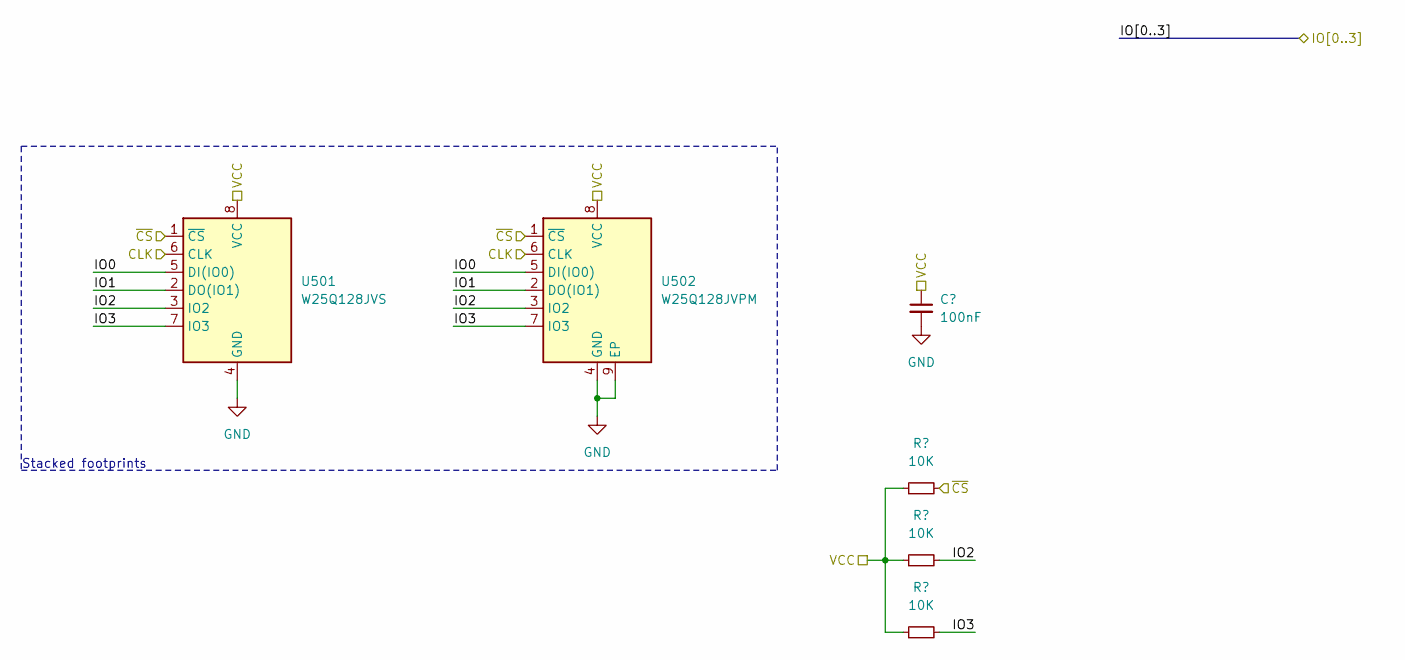
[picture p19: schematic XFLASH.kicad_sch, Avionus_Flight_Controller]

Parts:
C501: 100nF; C_0603_1608Metric
R501, R502, R503: 10K; R_0603_1608Metric
U501: W25Q128JVS; SOIC-8_5.23x5.23mm_P1.27mm
U502: W25Q128JVPM; WSON-8-1EP_6x5mm_P1.27mm_EP3.4x4.3mm

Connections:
/DEBUG/T_VCC: C501.1, R501.1, R502.1, R503.1, U501.8 (VCC), U502.8 (VCC); also elsewhere on the board
/MCU/QUADSPI_BK1_IO0: U501.5 (DI(IO0)), U502.5 (DI(IO0)); also elsewhere on the board
/MCU/QUADSPI_BK1_IO1: U501.2 (DO(IO1)), U502.2 (DO(IO1)); also elsewhere on the board
/MCU/QUADSPI_BK1_IO2: R502.2, U501.3 (IO2), U502.3 (IO2); also elsewhere on the board
/MCU/QUADSPI_BK1_IO3: R503.2, U501.7 (IO3), U502.7 (IO3); also elsewhere on the board
/MCU/QUADSPI_BK1_NCS: R501.2, U501.1 (~CS), U502.1 (~CS); also elsewhere on the board
/MCU/QUADSPI_CLK: U501.6 (CLK), U502.6 (CLK); also elsewhere on the board
GND: C501.2, U501.4 (GND), U502.4 (GND), U502.9 (EP); also elsewhere on the board

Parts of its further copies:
C601: 100nF; C_0603_1608Metric
R601, R602, R603: 10K; R_0603_1608Metric
U601: W25Q128JVS; SOIC-8_5.23x5.23mm_P1.27mm
U602: W25Q128JVPM; WSON-8-1EP_6x5mm_P1.27mm_EP3.4x4.3mm

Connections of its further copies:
/DEBUG/T_VCC: C601.1, R601.1, R602.1, R603.1, U601.8 (VCC), U602.8 (VCC); also elsewhere on the board
/MCU/QUADSPI_BK2_IO0: U601.5 (DI(IO0)), U602.5 (DI(IO0)); also elsewhere on the board
/MCU/QUADSPI_BK2_IO1: U601.2 (DO(IO1)), U602.2 (DO(IO1)); also elsewhere on the board
/MCU/QUADSPI_BK2_IO2: R602.2, U601.3 (IO2), U602.3 (IO2); also elsewhere on the board
/MCU/QUADSPI_BK2_IO3: R603.2, U601.7 (IO3), U602.7 (IO3); also elsewhere on the board
/MCU/QUADSPI_BK2_NCS: R601.2, U601.1 (~CS), U602.1 (~CS); also elsewhere on the board
/MCU/QUADSPI_CLK: U601.6 (CLK), U602.6 (CLK); also elsewhere on the board
GND: C601.2, U601.4 (GND), U602.4 (GND), U602.9 (EP); also elsewhere on the board

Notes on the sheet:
Stacked footprints

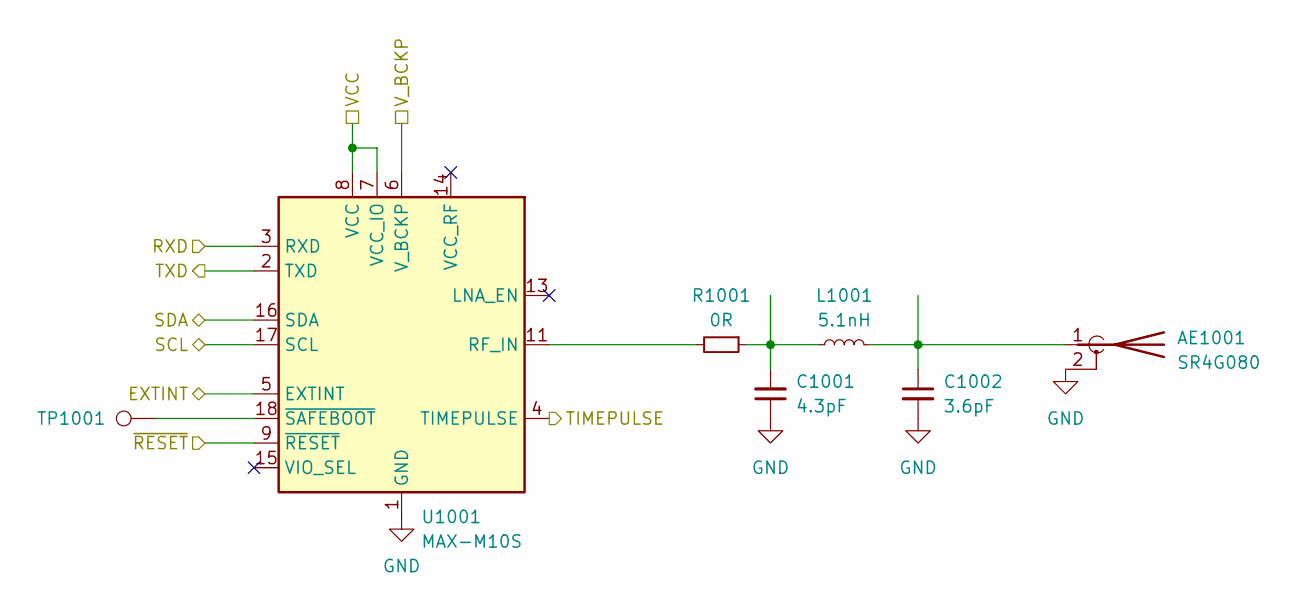
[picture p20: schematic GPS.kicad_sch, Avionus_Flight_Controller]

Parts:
AE1001: SR4G080
C1001: 4.3pF; C_0402_1005Metric_Pad0.74x0.62mm_HandSolder
C1002: 3.6pF; C_0402_1005Metric_Pad0.74x0.62mm_HandSolder
L1001: 5.1nH; L_0402_1005Metric_Pad0.77x0.64mm_HandSolder
R1001: 0R; R_0402_1005Metric_Pad0.72x0.64mm_HandSolder
TP1001: TestPoint_Pad_D1.0mm
U1001: MAX-M10S; ublox_MAX

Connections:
/GPS/EXTINT: U1001.5 (EXTINT); also elsewhere on the board
/GPS/RXD: U1001.3 (RXD); also elsewhere on the board
/GPS/SCL: U1001.17 (SCL); also elsewhere on the board
/GPS/SDA: U1001.16 (SDA); also elsewhere on the board
/GPS/TIMEPULSE: U1001.4 (TIMEPULSE); also elsewhere on the board
/GPS/TXD: U1001.2 (TXD); also elsewhere on the board
/GPS/VCC: U1001.7 (VCC_IO), U1001.8 (VCC); also elsewhere on the board
/GPS/V_BCKP: U1001.6 (V_BCKP); also elsewhere on the board
/GPS/~RESET: U1001.9 (~RESET); also elsewhere on the board
GND: AE1001.2 (Shield), C1001.1, C1002.2, U1001.1 (GND), U1001.10 (GND), U1001.12 (GND); also elsewhere on the board
unnamed: AE1001.1 (A), C1002.1, L1001.2
unnamed: C1001.2, L1001.1, R1001.1
unnamed: R1001.2, U1001.11 (RF_IN)
unnamed: TP1001.1, U1001.18 (~SAFEBOOT)

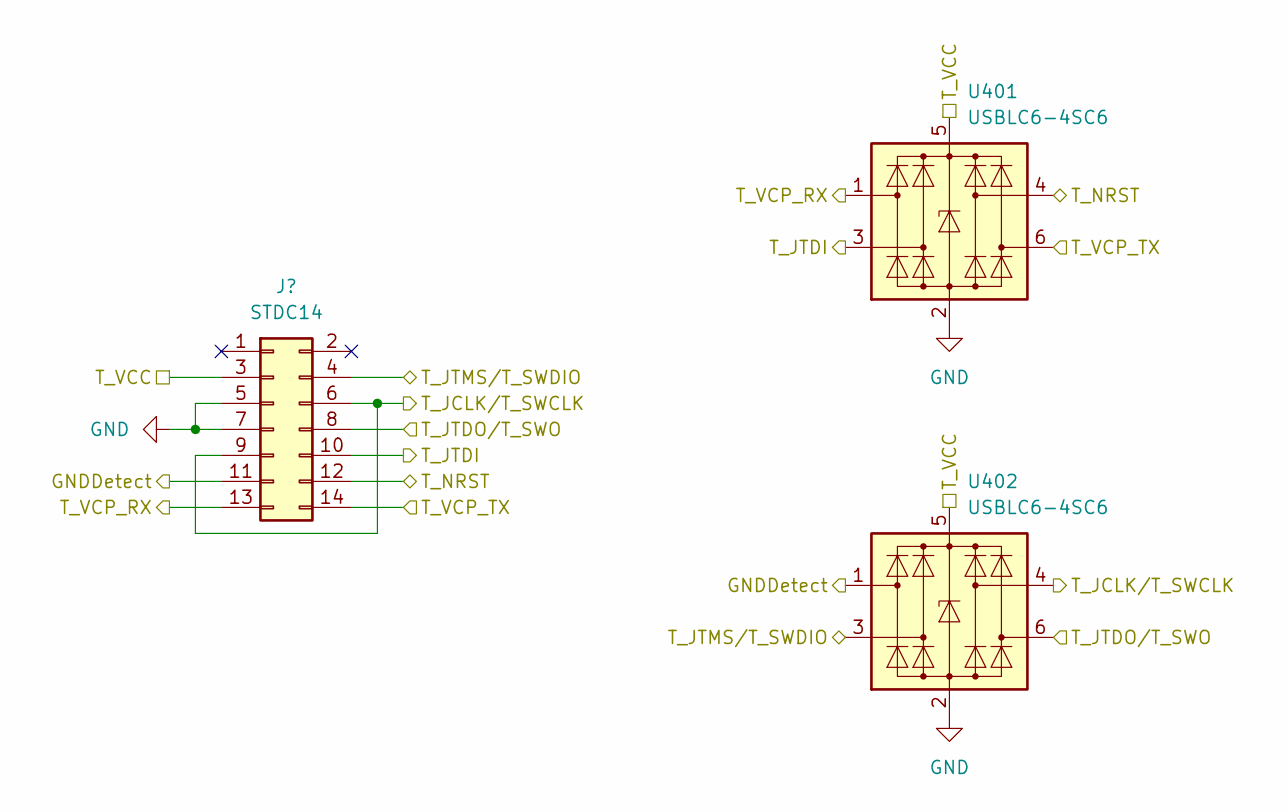
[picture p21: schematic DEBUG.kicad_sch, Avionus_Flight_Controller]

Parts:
J401: STDC14; FTSH-107-01-L-DV-K-A
U401, U402: USBLC6-4SC6; SOT-23-6

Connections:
/DEBUG/GNDDetect: J401.11, U402.1 (I/O1); also elsewhere on the board
/DEBUG/T_JCLK/T_SWCLK: J401.6, J401.9, U402.4 (I/O3); also elsewhere on the board
/DEBUG/T_JTDI: J401.10, U401.3 (I/O2); also elsewhere on the board
/DEBUG/T_JTDO/T_SWO: J401.8, U402.6 (I/O4); also elsewhere on the board
/DEBUG/T_JTMS/T_SWDIO: J401.4, U402.3 (I/O2); also elsewhere on the board
/DEBUG/T_NRST: J401.12, U401.4 (I/O3); also elsewhere on the board
/DEBUG/T_VCC: J401.3, U401.5 (VBUS), U402.5 (VBUS); also elsewhere on the board
/DEBUG/T_VCP_RX: J401.13, U401.1 (I/O1); also elsewhere on the board
/DEBUG/T_VCP_TX: J401.14, U401.6 (I/O4); also elsewhere on the board
GND: J401.5, J401.7, U401.2 (GND), U402.2 (GND); also elsewhere on the board

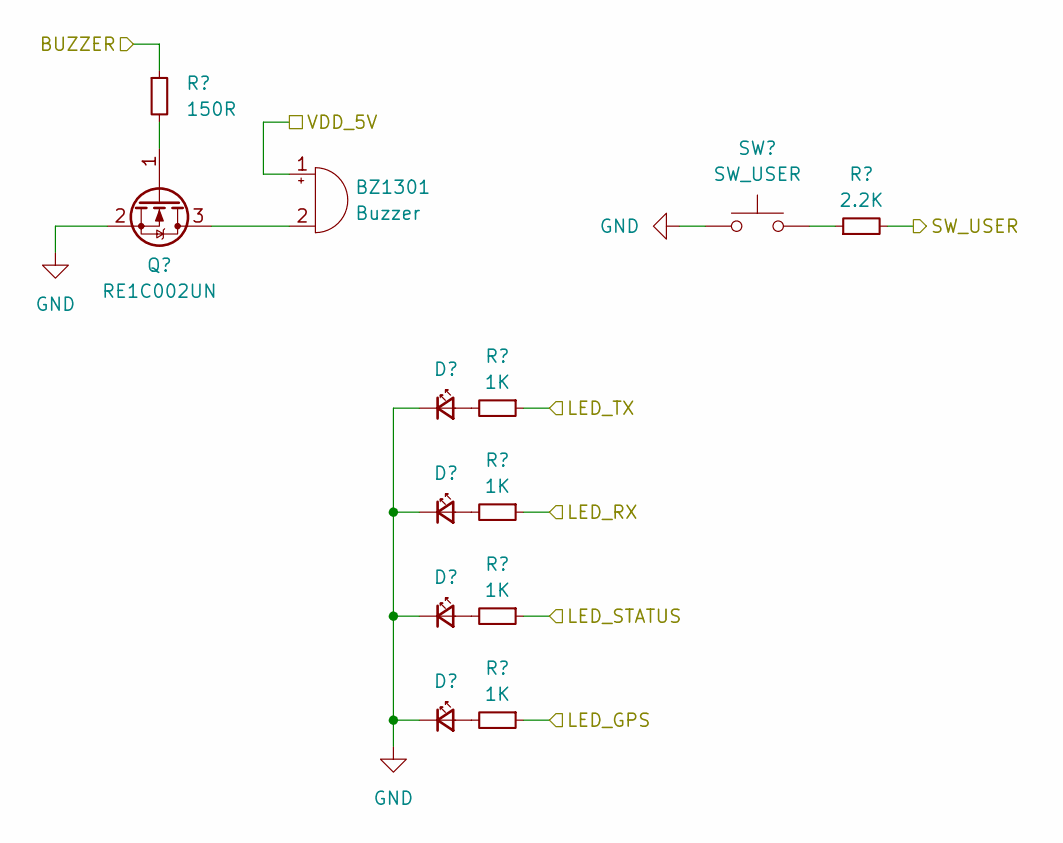
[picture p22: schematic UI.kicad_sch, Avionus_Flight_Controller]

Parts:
BZ1301: Buzzer; Buzzer_12x9.5RM7.6
D1301, D1302, D1303, D1304: LED_1206_3216Metric
Q1301: RE1C002UN; SOT-416
R1301: 150R; R_0603_1608Metric
R1302, R1303, R1304, R1305: 1K; R_0805_2012Metric
R1306: 2.2K; R_0805_2012Metric
SW1301: SW_USER; SW_PUSH_6mm_H5mm

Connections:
/MCU/GPIO_PD10: R1303.1; also elsewhere on the board
/MCU/GPIO_PD11: R1302.1; also elsewhere on the board
/MCU/GPIO_PE2: R1305.1; also elsewhere on the board
/MCU/GPIO_PE3: R1304.1; also elsewhere on the board
/MCU/GPIO_PF2+EXTI2: R1306.2; also elsewhere on the board
/MCU/TIM11_CH1: R1301.1; also elsewhere on the board
GND: D1301.1 (K), D1302.1 (K), D1303.1 (K), D1304.1 (K), Q1301.2 (S), SW1301.1; also elsewhere on the board
unnamed: BZ1301.2 (+), Q1301.3 (D)
unnamed: D1301.2 (A), R1302.2
unnamed: D1302.2 (A), R1303.2
unnamed: D1303.2 (A), R1304.2
unnamed: D1304.2 (A), R1305.2
unnamed: Q1301.1 (G), R1301.2
unnamed: R1306.1, SW1301.2

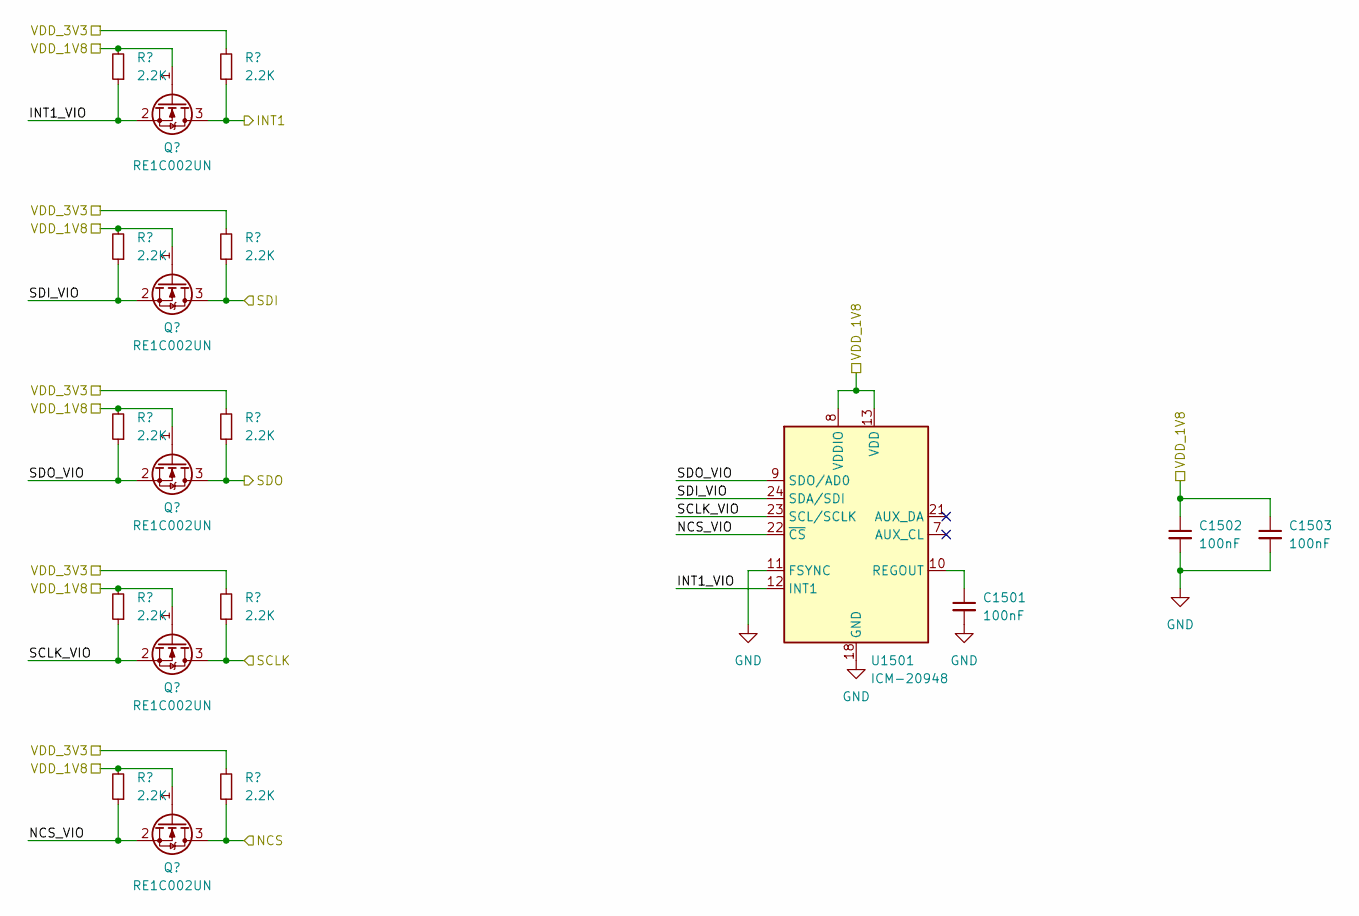
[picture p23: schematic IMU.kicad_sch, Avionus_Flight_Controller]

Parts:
C1501, C1502, C1503: 100nF; C_0603_1608Metric
Q1501, Q1502, Q1503, Q1504, Q1505: RE1C002UN; SOT-416
R1501, R1502, R1503, R1504, R1505, R1506, R1507, R1508, R1509, R1510: 2.2K; R_0805_2012Metric
U1501: ICM-20948; InvenSense_QFN-24_3x3mm_P0.4mm

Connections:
/GPS/VCC: R1506.2, R1507.2, R1508.2, R1509.2, R1510.2; also elsewhere on the board
/IMU/INT1: Q1501.3 (D), R1506.1; also elsewhere on the board
/IMU/INT1_VIO: Q1501.2 (S), R1501.1, U1501.12 (INT1)
/IMU/NCS: Q1505.3 (D), R1510.1; also elsewhere on the board
/IMU/NCS_VIO: Q1505.2 (S), R1505.1, U1501.22 (~CS)
/IMU/SCLK: Q1504.3 (D), R1509.1; also elsewhere on the board
/IMU/SCLK_VIO: Q1504.2 (S), R1504.1, U1501.23 (SCL/SCLK)
/IMU/SDI: Q1502.3 (D), R1507.1; also elsewhere on the board
/IMU/SDI_VIO: Q1502.2 (S), R1502.1, U1501.24 (SDA/SDI)
/IMU/SDO: Q1503.3 (D), R1508.1; also elsewhere on the board
/IMU/SDO_VIO: Q1503.2 (S), R1503.1, U1501.9 (SDO/AD0)
/IMU/VDD_1V8: C1502.1, C1503.1, Q1501.1 (G), Q1502.1 (G), Q1503.1 (G), Q1504.1 (G), Q1505.1 (G), R1501.2, R1502.2, R1503.2, R1504.2, R1505.2, U1501.8 (VDDIO), U1501.13 (VDD); also elsewhere on the board
GND: C1501.2, C1502.2, C1503.2, U1501.11 (FSYNC), U1501.18 (GND), U1501.20 (GND); also elsewhere on the board
unnamed: C1501.1, U1501.10 (REGOUT)

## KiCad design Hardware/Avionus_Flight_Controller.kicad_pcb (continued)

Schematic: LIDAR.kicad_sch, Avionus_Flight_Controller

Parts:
J1401: LIDAR1; PinHeader_1x08_P2.54mm_Horizontal
J1402: LIDAR2; PinHeader_1x06_P2.54mm_Horizontal
U801: USBLC6-2SC6; SOT-23-6
U1401: USBLC6-4SC6; SOT-23-6

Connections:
/GPS/SCL: J1401.1, J1402.3, U1401.6 (I/O4); also elsewhere on the board
/GPS/SDA: J1401.2, J1402.4, U1401.4 (I/O3); also elsewhere on the board
/LIDAR/RX: J1401.6, U1401.1 (I/O1); also elsewhere on the board
/LIDAR/TX/DATA_READY: J1401.5, U1401.3 (I/O2); also elsewhere on the board
/USB_D+: U801.1 (I/O1); also elsewhere on the board
/USB_D-: U801.3 (I/O2); also elsewhere on the board
GND: J1401.3, J1401.7, J1402.2, U801.2 (GND), U1401.2 (GND); also elsewhere on the board

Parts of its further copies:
U1402: USBLC6-2SC6; SOT-23-6

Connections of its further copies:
/LIDAR/GPIO1: U1402.1 (I/O1); also elsewhere on the board
/LIDAR/XSHUT: U1402.3 (I/O2); also elsewhere on the board
GND: U1402.2 (GND); also elsewhere on the board

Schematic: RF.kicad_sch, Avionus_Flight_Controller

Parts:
J901: SMA_Amphenol_132134_Vertical
U901: LAMBDA62

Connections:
/MCU/GPIO_PB10+EXTI10: U901.7 (DIO1); also elsewhere on the board
/MCU/GPIO_PB11+EXTI11: U901.8 (DIO2); also elsewhere on the board
/MCU/GPIO_PB12+EXTI12: U901.9 (DIO3); also elsewhere on the board
/MCU/GPIO_PE11: U901.16 (NSS); also elsewhere on the board
/MCU/GPIO_PE15+EXTI15: U901.6 (BUSY); also elsewhere on the board
/MCU/GPIO_PF13: U901.4 (RX_SWITCH); also elsewhere on the board
/MCU/GPIO_PF14: U901.5 (TX_SWITCH); also elsewhere on the board
/MCU/GPIO_PF15: U901.12 (~RESET); also elsewhere on the board
/MCU/SPI4_MISO: U901.14 (MISO); also elsewhere on the board
/MCU/SPI4_MOSI: U901.15 (MOSI); also elsewhere on the board
/MCU/SPI4_SCK: U901.13 (SCK); also elsewhere on the board
/POWER/D4_3V3: U901.3 (VCC); also elsewhere on the board
GND: J901.2 (Ext), U901.2 (GND); also elsewhere on the board
unnamed: J901.1 (In), U901.1 (ANT/NC)

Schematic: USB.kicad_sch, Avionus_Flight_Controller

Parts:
J801: USB_C_Receptacle_USB2.0; USB4110-GF-A
R801, R802: 5.1K; R_0603_1608Metric
TP801: TestPoint_Pad_D1.0mm
U801: USBLC6-2SC6; SOT-23-6

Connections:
/MCU/USB_OTG_HS_SOF: TP801.1; also elsewhere on the board
/USB_D+: U801.1 (I/O1); also elsewhere on the board
/USB_D-: U801.3 (I/O2); also elsewhere on the board
GND: J801.A1 (GND), J801.A12 (GND), J801.B1 (GND), J801.B12 (GND), R801.1, R802.1, U801.2 (GND); also elsewhere on the board
unnamed: J801.A5 (CC1), R801.2
unnamed: J801.B5 (CC2), R802.2

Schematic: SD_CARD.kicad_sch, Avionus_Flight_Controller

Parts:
C701: 100nF; C_0603_1608Metric
J701: SD_Card; SDP-09L-SG
R701, R702, R703, R704, R705: 47K; R_0805_2012Metric
R706, R707: 2.2K; R_0805_2012Metric

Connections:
/MCU/GPIO_PG13+EXTI13: R706.2; also elsewhere on the board
/MCU/GPIO_PG14: R707.1; also elsewhere on the board
/MCU/SDMMC2_CK: J701.5 (CLK); also elsewhere on the board
/MCU/SDMMC2_CMD: J701.2 (CMD), R703.2; also elsewhere on the board
/MCU/SDMMC2_D0: J701.7 (DAT0), R702.2; also elsewhere on the board
/MCU/SDMMC2_D1: J701.8 (DAT1), R701.2; also elsewhere on the board
/MCU/SDMMC2_D2: J701.9 (DAT2), R705.2; also elsewhere on the board
/MCU/SDMMC2_D3: J701.1 (CD/DAT3), R704.2; also elsewhere on the board
/POWER/D3_3V3: C701.1, J701.4 (VDD), R701.1, R702.1, R703.1, R704.1, R705.1; also elsewhere on the board
GND: C701.2, J701.3 (VSS), J701.6 (VSS), J701.12 (SHELL1), J701.13 (SHELL2); also elsewhere on the board
unnamed: J701.10 (CARD_DETECT), R706.1
unnamed: J701.11 (WRITE_PROTECT), R707.2

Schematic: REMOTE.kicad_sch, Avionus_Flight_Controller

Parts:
J1101: PPM; PinHeader_1x03_P2.54mm_Horizontal
J1102: iBUS; PinHeader_1x03_P2.54mm_Horizontal
Q1101, Q1102: RE1C002UN; SOT-416
R1101, R1102, R1103, R1104: 2.2K; R_0805_2012Metric
U1101: USBLC6-4SC6; SOT-23-6

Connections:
/DEBUG/T_VCC: Q1101.1 (G), Q1102.1 (G), R1101.2, R1102.2; also elsewhere on the board
/MCU/TIM9_CH2: Q1101.2 (S), R1101.1; also elsewhere on the board
/MCU/UART4_TX: Q1102.2 (S), R1102.1; also elsewhere on the board
GND: J1101.1, J1102.1, U1101.2 (GND); also elsewhere on the board
unnamed: J1101.3, Q1101.3 (D), R1103.1, U1101.1 (I/O1)
unnamed: J1102.3, Q1102.3 (D), R1104.1, U1101.3 (I/O2)

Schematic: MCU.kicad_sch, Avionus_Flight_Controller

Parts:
C301, C302: 15pF; C_0805_2012Metric
C303, C304: 2.2uF; C_0805_2012Metric
C305, C306, C307, C308, C309, C310, C311, C312, C313, C314, C315, C316, C318, C319: 100nF; C_0603_1608Metric
C317: 4.7uF; C_1206_3216Metric
C320, C321: 1uF; C_0805_2012Metric
R301, R302, R303, R304: 10K; R_0603_1608Metric
SW301: RESET; SW_PUSH_6mm_H5mm
TP301, TP302, TP303, TP304, TP305, TP306, TP307, TP308, TP309, TP310: TestPoint_Pad_D1.0mm
U301: STM32F722ZETx; LQFP-144_20x20mm_P0.5mm
Y301: 24MHz; ATS240C

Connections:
/DEBUG/GNDDetect: U301.104 (PA12); also elsewhere on the board
/DEBUG/T_JCLK/T_SWCLK: U301.109 (PA14); also elsewhere on the board
/DEBUG/T_JTDI: U301.110 (PA15); also elsewhere on the board
/DEBUG/T_JTDO/T_SWO: U301.133 (PB3); also elsewhere on the board
/DEBUG/T_JTMS/T_SWDIO: U301.105 (PA13); also elsewhere on the board
/DEBUG/T_NRST: C319.2, SW301.2, U301.25 (NRST); also elsewhere on the board
/DEBUG/T_VCC: C305.1, C306.1, C307.1, C308.1, C309.1, C310.1, C311.1, C312.1, C313.1, C314.1, C315.1, C316.1, C317.1, C318.1, C320.1, C321.1, U301.17 (VDD), U301.30 (VDD), U301.32 (VREF+), U301.33 (VDDA), U301.39 (VDD), U301.52 (VDD), U301.62 (VDD), U301.72 (VDD), U301.84 (VDD), U301.95 (VDDUSB), U301.108 (VDD), U301.121 (VDDSDMMC), U301.131 (VDD), U301.143 (PDR_ON), U301.144 (VDD); also elsewhere on the board
/DEBUG/T_VCP_RX: U301.78 (PD9); also elsewhere on the board
/DEBUG/T_VCP_TX: U301.77 (PD8); also elsewhere on the board
/GPS/EXTINT: U301.118 (PD4); also elsewhere on the board
/GPS/RXD: U301.113 (PC12); also elsewhere on the board
/GPS/SCL: U301.11 (PF1); also elsewhere on the board
/GPS/SDA: U301.10 (PF0); also elsewhere on the board
/GPS/TIMEPULSE: U301.117 (PD3); also elsewhere on the board
/GPS/TXD: U301.116 (PD2); also elsewhere on the board
/GPS/V_BCKP: U301.6 (VBAT); also elsewhere on the board
/GPS/~RESET: U301.114 (PD0); also elsewhere on the board
/IMU/INT1: U301.57 (PG1); also elsewhere on the board
/IMU/NCS: U301.56 (PG0); also elsewhere on the board
/IMU/SCLK: U301.41 (PA5); also elsewhere on the board
/IMU/SDI: U301.43 (PA7); also elsewhere on the board
/IMU/SDO: U301.42 (PA6); also elsewhere on the board
/LIDAR/GPIO1: U301.93 (PG8); also elsewhere on the board
/LIDAR/RX: U301.142 (PE1); also elsewhere on the board
/LIDAR/TX/DATA_READY: U301.141 (PE0); also elsewhere on the board
/LIDAR/XSHUT: U301.92 (PG7); also elsewhere on the board
/MCU/ADC1_IN12: U301.28 (PC2); also elsewhere on the board
/MCU/ADC1_IN14: U301.44 (PC4); also elsewhere on the board
/MCU/ADC2_IN10: U301.26 (PC0); also elsewhere on the board
/MCU/ADC2_IN11: U301.27 (PC1); also elsewhere on the board
/MCU/ADC2_IN13: U301.29 (PC3); also elsewhere on the board
/MCU/ADC2_IN15: U301.45 (PC5); also elsewhere on the board
/MCU/ADC3_IN8: U301.22 (PF10); also elsewhere on the board
/MCU/ADC3_IN9: U301.13 (PF3); also elsewhere on the board
/MCU/ADC3_IN14: U301.14 (PF4); also elsewhere on the board
/MCU/ADC3_IN15: U301.15 (PF5); also elsewhere on the board
/MCU/BOOT0: R304.1, U301.138 (BOOT0)
/MCU/GPIO_PB10+EXTI10: U301.69 (PB10); also elsewhere on the board
/MCU/GPIO_PB11+EXTI11: U301.70 (PB11); also elsewhere on the board
/MCU/GPIO_PB12+EXTI12: U301.73 (PB12); also elsewhere on the board
/MCU/GPIO_PD10: U301.79 (PD10); also elsewhere on the board
/MCU/GPIO_PD11: U301.80 (PD11); also elsewhere on the board
/MCU/GPIO_PE2: U301.1 (PE2); also elsewhere on the board
/MCU/GPIO_PE3: U301.2 (PE3); also elsewhere on the board
/MCU/GPIO_PE4: U301.3 (PE4); also elsewhere on the board
/MCU/GPIO_PE5+EXTI5: U301.4 (PE5); also elsewhere on the board
/MCU/GPIO_PE11: U301.64 (PE11); also elsewhere on the board
/MCU/GPIO_PE15+EXTI15: U301.68 (PE15); also elsewhere on the board
/MCU/GPIO_PF2+EXTI2: U301.12 (PF2); also elsewhere on the board
/MCU/GPIO_PF11: U301.49 (PF11); also elsewhere on the board
/MCU/GPIO_PF12: U301.50 (PF12); also elsewhere on the board
/MCU/GPIO_PF13: U301.53 (PF13); also elsewhere on the board
/MCU/GPIO_PF14: U301.54 (PF14); also elsewhere on the board
/MCU/GPIO_PF15: U301.55 (PF15); also elsewhere on the board
/MCU/GPIO_PG4: U301.89 (PG4); also elsewhere on the board
/MCU/GPIO_PG5: U301.90 (PG5); also elsewhere on the board
/MCU/GPIO_PG6+EXTI6: U301.91 (PG6); also elsewhere on the board
/MCU/GPIO_PG13+EXTI13: U301.128 (PG13); also elsewhere on the board
/MCU/GPIO_PG14: U301.129 (PG14); also elsewhere on the board
/MCU/GPIO_PG15: U301.132 (PG15); also elsewhere on the board
/MCU/LOOP: R301.1, R302.1
/MCU/QUADSPI_BK1_IO0: U301.20 (PF8); also elsewhere on the board
/MCU/QUADSPI_BK1_IO1: U301.21 (PF9); also elsewhere on the board
/MCU/QUADSPI_BK1_IO2: U301.19 (PF7); also elsewhere on the board
/MCU/QUADSPI_BK1_IO3: U301.18 (PF6); also elsewhere on the board
/MCU/QUADSPI_BK1_NCS: U301.136 (PB6); also elsewhere on the board
/MCU/QUADSPI_BK2_IO0: U301.58 (PE7); also elsewhere on the board
/MCU/QUADSPI_BK2_IO1: U301.59 (PE8); also elsewhere on the board
/MCU/QUADSPI_BK2_IO2: U301.60 (PE9); also elsewhere on the board
/MCU/QUADSPI_BK2_IO3: U301.63 (PE10); also elsewhere on the board
/MCU/QUADSPI_BK2_NCS: U301.112 (PC11); also elsewhere on the board
/MCU/QUADSPI_CLK: U301.48 (PB2); also elsewhere on the board
/MCU/RTC_OUT: U301.7 (PC13); also elsewhere on the board
/MCU/SDMMC2_CK: U301.122 (PD6); also elsewhere on the board
/MCU/SDMMC2_CMD: U301.123 (PD7); also elsewhere on the board
/MCU/SDMMC2_D0: U301.124 (PG9); also elsewhere on the board
/MCU/SDMMC2_D1: U301.125 (PG10); also elsewhere on the board
/MCU/SDMMC2_D2: U301.126 (PG11); also elsewhere on the board
/MCU/SDMMC2_D3: U301.127 (PG12); also elsewhere on the board
/MCU/SPI4_MISO: U301.66 (PE13); also elsewhere on the board
/MCU/SPI4_MOSI: U301.67 (PE14); also elsewhere on the board
/MCU/SPI4_SCK: U301.65 (PE12); also elsewhere on the board
/MCU/TIM9_CH2: U301.5 (PE6); also elsewhere on the board
/MCU/TIM11_CH1: U301.140 (PB9); also elsewhere on the board
/MCU/UART4_TX: U301.111 (PC10); also elsewhere on the board
/MCU/USB_OTG_HS_SOF: U301.40 (PA4); also elsewhere on the board
/SERVO/CH0: U301.96 (PC6); also elsewhere on the board
/SERVO/CH1: U301.97 (PC7); also elsewhere on the board
/SERVO/CH2: U301.98 (PC8); also elsewhere on the board
/SERVO/CH3: U301.99 (PC9); also elsewhere on the board
/SERVO/CH4: U301.82 (PD13); also elsewhere on the board
/SERVO/CH5: U301.81 (PD12); also elsewhere on the board
/SERVO/CH6: U301.85 (PD14); also elsewhere on the board
/SERVO/CH7: U301.86 (PD15); also elsewhere on the board
/SERVO/CH8: U301.100 (PA8); also elsewhere on the board
/SERVO/CH9: U301.101 (PA9); also elsewhere on the board
/SERVO/CH10: U301.102 (PA10); also elsewhere on the board
/SERVO/CH11: U301.103 (PA11); also elsewhere on the board
/SERVO/CH12: U301.37 (PA3); also elsewhere on the board
/SERVO/CH13: U301.36 (PA2); also elsewhere on the board
/SERVO/CH14: U301.35 (PA1); also elsewhere on the board
/SERVO/CH15: U301.34 (PA0); also elsewhere on the board
/USB_D+: U301.76 (PB15); also elsewhere on the board
/USB_D-: U301.75 (PB14); also elsewhere on the board
GND: C301.1, C302.1, C303.1, C304.1, C305.2, C306.2, C307.2, C308.2, C309.2, C310.2, C311.2, C312.2, C313.2, C314.2, C315.2, C316.2, C317.2, C318.2, C319.1, C320.2, C321.2, R304.2, SW301.1, U301.16 (VSS), U301.31 (VSSA), U301.38 (VSS), U301.51 (VSS), U301.61 (VSS), U301.83 (VSS), U301.94 (VSS), U301.107 (VSS), U301.120 (VSS), U301.130 (VSS); also elsewhere on the board
unnamed: TP303.1, U301.46 (PB0)
unnamed: TP304.1, U301.47 (PB1)
unnamed: TP305.1, U301.134 (PB4)
unnamed: TP306.1, U301.135 (PB5)
unnamed: TP307.1, U301.137 (PB7)
unnamed: TP308.1, U301.139 (PB8)
unnamed: R303.2, U301.74 (PB13)
unnamed: R301.2, U301.8 (PC14)
unnamed: R302.2, U301.9 (PC15)
unnamed: TP309.1, U301.115 (PD1)
unnamed: TP310.1, U301.119 (PD5)
unnamed: TP301.1, U301.87 (PG2)
unnamed: TP302.1, U301.88 (PG3)
unnamed: C301.2, U301.23 (PH0), Y301.2
unnamed: C302.2, U301.24 (PH1), Y301.1
unnamed: C303.2, U301.71 (VCAP_1)
unnamed: C304.2, U301.106 (VCAP_2)

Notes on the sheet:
VDDSDMMC
VDD
VDDA

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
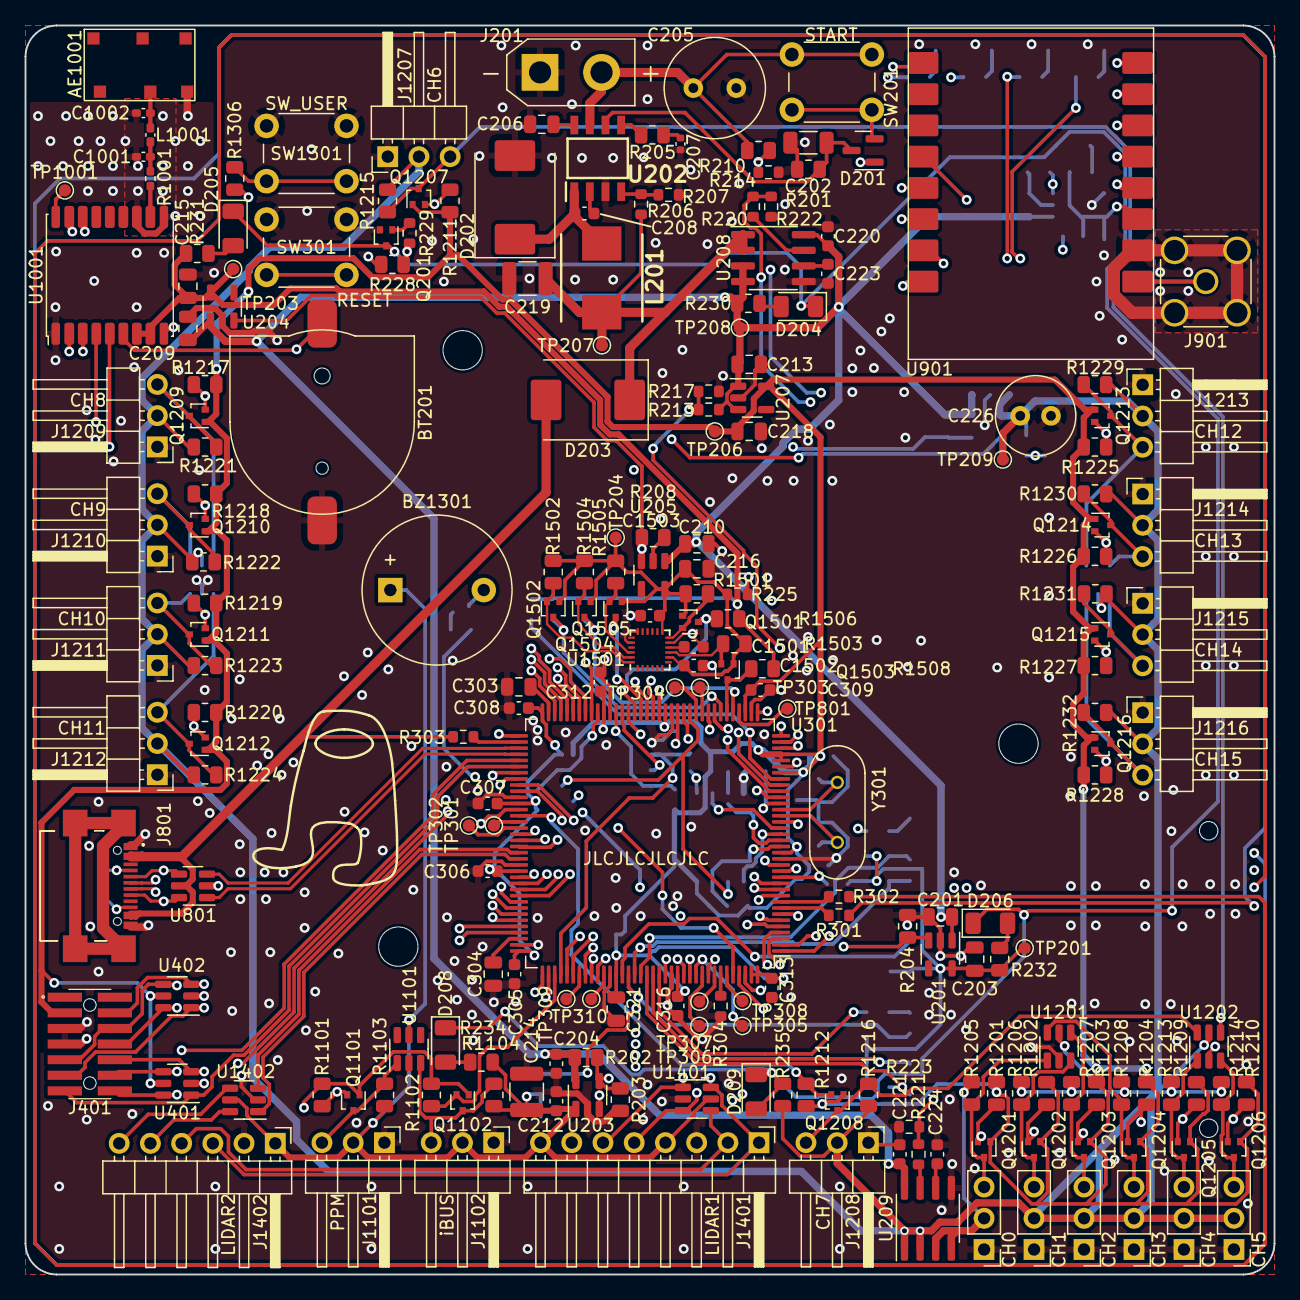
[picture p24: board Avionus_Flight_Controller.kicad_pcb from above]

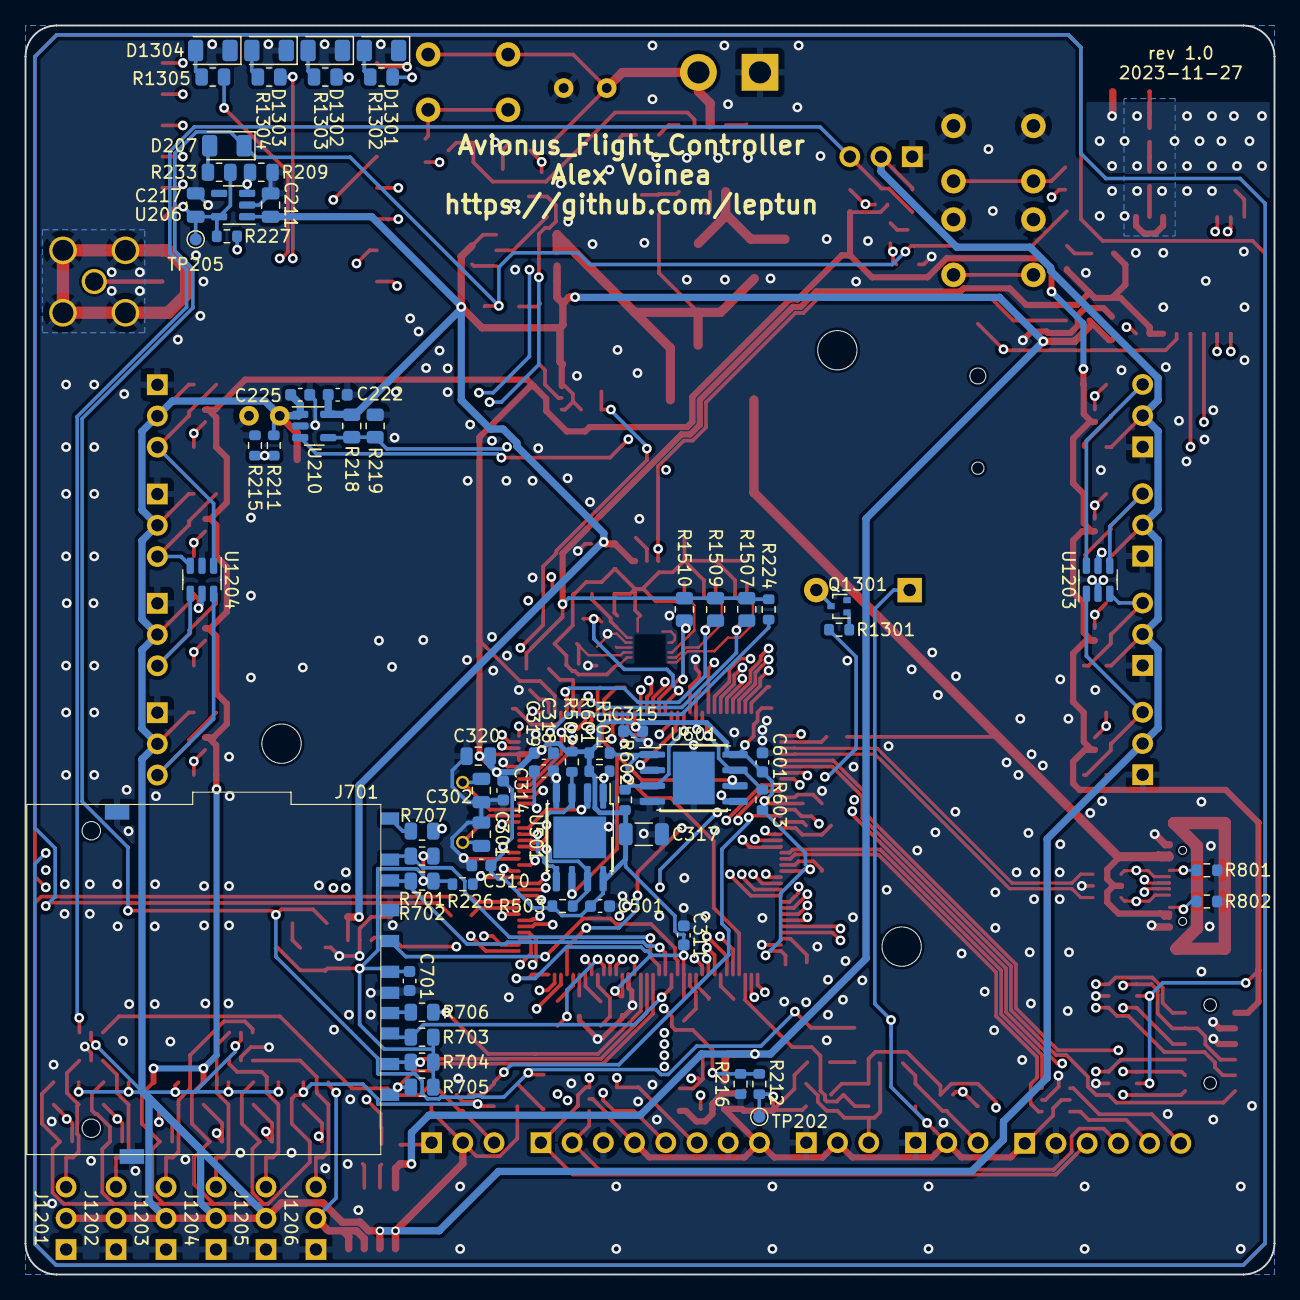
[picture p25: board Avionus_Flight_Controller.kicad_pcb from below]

Board: 4 copper layers, 101.6 x 101.6 mm, 287 parts (68 on the bottom side), 197 nets.

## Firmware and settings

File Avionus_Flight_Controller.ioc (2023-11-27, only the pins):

Mcu.UserName=STM32F722ZETx
PA0-WKUP.Signal=S_TIM2_CH1_ETR
PA1.Signal=S_TIM2_CH2
PA10.Signal=S_TIM1_CH3
PA11.Signal=S_TIM1_CH4
PA12.GPIO_Label=DEBUG_GNDDetect
PA12.Signal=GPIO_Input
PA13.Signal=SYS_JTMS-SWDIO
PA14.Signal=SYS_JTCK-SWCLK
PA15.Signal=SYS_JTDI
PA2.Signal=S_TIM2_CH3
PA3.Signal=S_TIM2_CH4
PA4.Signal=USB_OTG_HS_SOF
PA5.Signal=SPI1_SCK
PA6.Signal=SPI1_MISO
PA7.Signal=SPI1_MOSI
PA8.Signal=S_TIM1_CH1
PA9.Signal=S_TIM1_CH2
PB10.GPIO_Label=RF_DIO1
PB10.Signal=GPXTI10
PB11.GPIO_Label=RF_DIO2
PB11.Signal=GPXTI11
PB12.GPIO_Label=RF_DIO3
PB12.Signal=GPXTI12
PB13.Signal=USB_OTG_HS_VBUS
PB14.Signal=USB_OTG_HS_DM
PB15.Signal=USB_OTG_HS_DP
PB2.Signal=QUADSPI_CLK
PB3.Signal=SYS_JTDO-SWO
PB6.Signal=QUADSPI_BK1_NCS
PB9.GPIO_Label=UI_BUZZER
PB9.Signal=S_TIM11_CH1
PC0.Signal=SharedAnalog_PC0
PC1.Signal=SharedAnalog_PC1
PC10.GPIO_Label=REMOTE_iBUS
PC10.Signal=UART4_TX
PC11.Signal=QUADSPI_BK2_NCS
PC12.GPIO_Label=GPS_TX
PC12.Signal=UART5_TX
PC13.GPIO_Label=POWER_D1_EN
PC13.Signal=RTC_OUT
PC14-OSC32_IN.GPIO_Label=FAULT_DET_IN
PC14-OSC32_IN.Signal=GPIO_Input
PC15-OSC32_OUT.GPIO_Label=FAULT_DET_OUT
PC15-OSC32_OUT.Signal=GPIO_Output
PC2.Signal=SharedAnalog_PC2
PC3.Signal=SharedAnalog_PC3
PC4.Signal=SharedAnalog_PC4
PC5.Signal=SharedAnalog_PC5
PC6.Signal=SharedStack_PC6
PC7.Signal=S_TIM3_CH2
PC8.Signal=S_TIM3_CH3
PC9.Signal=S_TIM3_CH4
PD0.GPIO_Label=GPS_NRESET
PD0.Signal=GPIO_Output
PD10.GPIO_Label=UI_LED_RX
PD10.Signal=GPIO_Output
PD11.GPIO_Label=UI_LED_TX
PD11.Signal=GPIO_Output
PD12.Signal=S_TIM4_CH1
PD13.Signal=S_TIM4_CH2
PD14.Signal=S_TIM4_CH3
PD15.Signal=S_TIM4_CH4
PD2.GPIO_Label=GPS_RX
PD2.Signal=UART5_RX
PD3.GPIO_Label=GPS_TIMEPULSE
PD3.Signal=GPXTI3
PD4.GPIO_Label=GPS_EXTINT
PD4.Signal=GPXTI4
PD6.Signal=SDMMC2_CK
PD7.Signal=SDMMC2_CMD
PD8.GPIO_Label=DEBUG_TX
PD8.Signal=USART3_TX
PD9.GPIO_Label=DEBUG_RX
PD9.Signal=USART3_RX
PE0.GPIO_Label=LIDAR_RX
PE0.Signal=SharedStack_PE0
PE1.GPIO_Label=LIDAR_TX
PE1.Signal=UART8_TX
PE10.Signal=QUADSPI_BK2_IO3
PE11.GPIO_Label=RF_NSS
PE11.Signal=GPIO_Output
PE12.Signal=SPI4_SCK
PE13.Signal=SPI4_MISO
PE14.Signal=SPI4_MOSI
PE15.GPIO_Label=RF_BUSY
PE15.Signal=GPXTI15
PE2.GPIO_Label=UI_LED_GPS
PE2.Signal=GPIO_Output
PE3.GPIO_Label=UI_LED_STATUS
PE3.Signal=GPIO_Output
PE4.GPIO_Label=POWER_D5_EN
PE4.Signal=GPIO_Output
PE5.GPIO_Label=POWER_D5_nFAULT
PE5.Signal=GPXTI5
PE6.GPIO_Label=REMOTE_PPM
PE6.Signal=S_TIM9_CH2
PE7.Signal=QUADSPI_BK2_IO0
PE8.Signal=QUADSPI_BK2_IO1
PE9.Signal=QUADSPI_BK2_IO2
PF0.Signal=I2C2_SDA
PF1.Signal=I2C2_SCL
PF10.Signal=SharedAnalog_PF10
PF11.GPIO_Label=POWER_D2_EN
PF11.Signal=GPIO_Output
PF12.GPIO_Label=POWER_D4_EN
PF12.Signal=GPIO_Output
PF13.GPIO_Label=RF_RX_SWITCH
PF13.Signal=GPIO_Output
PF14.GPIO_Label=RF_TX_SWITCH
PF14.Signal=GPIO_Output
PF15.GPIO_Label=RF_NRESET
PF15.Signal=GPIO_Output
PF2.GPIO_Label=UI_SW_USER
PF2.Signal=GPXTI2
PF3.Signal=SharedAnalog_PF3
PF4.Signal=SharedAnalog_PF4
PF5.Signal=SharedAnalog_PF5
PF6.Signal=QUADSPI_BK1_IO3
PF7.Signal=QUADSPI_BK1_IO2
PF8.Signal=QUADSPI_BK1_IO0
PF9.Signal=QUADSPI_BK1_IO1
PG0.GPIO_Label=IMU_NSS
PG0.Signal=GPIO_Output
PG1.GPIO_Label=IMU_INT1
PG1.Signal=GPXTI1
PG10.Signal=SDMMC2_D1
PG11.Signal=SDMMC2_D2
PG12.Signal=SDMMC2_D3
PG13.GPIO_Label=SD_CD
PG13.Signal=GPXTI13
PG14.GPIO_Label=SD_WP
PG14.Signal=GPIO_Input
PG15.GPIO_Label=POWER_D3_EN
PG15.Signal=GPIO_Output
PG4.GPIO_Label=POWER_LEDs_EN
PG4.Signal=GPIO_Output
PG5.GPIO_Label=POWER_SERVO_5V_AUX_EN
PG5.Signal=GPIO_Output
PG6.GPIO_Label=POWER_SERVO_5V_AUX_nFAULT
PG6.Signal=GPXTI6
PG7.GPIO_Label=LIDAR_XSHUT
PG7.Signal=GPIO_Output
PG8.GPIO_Label=LIDAR_GPIO1
PG8.Signal=GPXTI8
PG9.Signal=SDMMC2_D0
PH0-OSC_IN.Signal=RCC_OSC_IN
PH1-OSC_OUT.Signal=RCC_OSC_OUT

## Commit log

2023-08-23 update kicadlibs
2023-08-24 Add stacked footprints graphic
    [XFLASH.kicad_sch]
2023-08-25 ERC fixes
    [DEBUG.kicad_sch, MCU.kicad_sch, POWER.kicad_sch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]
2023-08-25 beautify USB
    [USB.kicad_sch]
2023-08-25 Update Buck converter compensation circuitry
    [POWER.kicad_sch]
2023-08-25 Add power documentation
    [POWER.kicad_sch]
2023-08-25 Add IMU supply capacitors
    [IMU.kicad_sch]
2023-08-28 Fix RF crystal frequency
    [RF.kicad_sch]
2023-08-28 IMU FSYNC to GND
    [IMU.kicad_sch]
2023-10-09 Checkpoint routing
    [Avionus_Flight_Controller.kicad_pcb, Avionus_Flight_Controller.kicad_sch]
2023-10-27 Finalize schematic and some more routing
    [Avionus_Flight_Controller.kicad_pcb, Avionus_Flight_Controller.kicad_sch, POWER.kicad_sch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]
2023-11-02 Misc routing
    [Avionus_Flight_Controller.kicad_pcb, MCU.kicad_sch, POWER.kicad_sch]
2023-11-09 Finalize RF
    [Avionus_Flight_Controller.kicad_pcb, RF.kicad_sch]
2023-11-09 Lots of routing
    [Avionus_Flight_Controller.kicad_pcb, Avionus_Flight_Controller.kicad_sch]
2023-11-09 More routing
    [Avionus_Flight_Controller.kicad_pcb, Avionus_Flight_Controller.kicad_sch, MCU.kicad_sch]
2023-11-09 Fix overlapping courtyards
    [Avionus_Flight_Controller.kicad_pcb]
2023-11-11 Schematic layout fixes
    [Avionus_Flight_Controller.kicad_pcb, Avionus_Flight_Controller.kicad_sch, MCU.kicad_sch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]
2023-11-11 Finalize routing
    [Avionus_Flight_Controller.kicad_pcb, MCU.kicad_sch, USB.kicad_sch]
2023-11-11 Misc fixes
    [Avionus_Flight_Controller.kicad_pcb, Avionus_Flight_Controller.kicad_sch]
2023-11-14 Add lidar2
    [Avionus_Flight_Controller.kicad_pcb, Avionus_Flight_Controller.kicad_sch, DEBUG.kicad_sch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]
2023-11-14 Small layout fix
    [Avionus_Flight_Controller.kicad_pcb]
2023-11-15 Change 12K resistor to 10K
    [Avionus_Flight_Controller.kicad_pcb, POWER.kicad_sch]
2023-11-15 Change from 5V_SEL to VBUS diode
    [Avionus_Flight_Controller.kicad_pcb, POWER.kicad_sch]
2023-11-18 Add mounting holes
    [Avionus_Flight_Controller.kicad_pcb, Avionus_Flight_Controller.kicad_sch]
2023-11-25 Finalize silkscreen
    [Avionus_Flight_Controller.kicad_pcb, Avionus_Flight_Controller.kicad_sch, DEBUG.kicad_sch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]
2023-11-25 Add "JLCJLCJLCJLC" text
    [Avionus_Flight_Controller.kicad_pcb]
2023-11-25 Add GND vias
    [Avionus_Flight_Controller.kicad_pcb]
2023-11-26 Move via from under screw head
    [Avionus_Flight_Controller.kicad_pcb]
2023-11-26 Minor routing improvements
    [Avionus_Flight_Controller.kicad_pcb]
2023-11-27 Fix UART8 disabled for no reason in ioc file
    [Avionus_Flight_Controller.ioc]
2023-11-27 Minor root sheet layout fixes
    [Avionus_Flight_Controller.kicad_sch]
2023-11-27 Swap ADC connections for simultaneous power measurement
    [Avionus_Flight_Controller.kicad_pcb, Avionus_Flight_Controller.kicad_sch, MCU.kicad_sch]
2023-11-27 Fix buzzer polarity and UI power domain notation
    [Avionus_Flight_Controller.kicad_sch, POWER.kicad_sch, UI.kicad_sch]
2023-11-27 Update release date
    [Avionus_Flight_Controller.kicad_pcb, Avionus_Flight_Controller.kicad_sch, DEBUG.kicad_sch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]
2023-11-27 Plot output files
    [Avionus_Flight_Controller-B_Cu.gbl, Avionus_Flight_Controller-B_Mask.gbs, Avionus_Flight_Controller-B_Paste.gbp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]
2023-11-27 Plot schematic PDF
2023-12-20 Development backplate
    [Avionus development backplate.SLDPRT, Avionus development backplate.STL]
